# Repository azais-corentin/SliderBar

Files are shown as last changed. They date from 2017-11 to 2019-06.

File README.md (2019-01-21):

<p align="center">
  <a href="https://github.com/Haellsigh/SliderBar">
    
  </a>

  <h3 align="center">SliderBar</h3>

  <p align="center">
    Motorized keyboard slider with an advanced controller.
  </p>
</p>

## Table of contents

- [What's that](#whats-that)
- [Quick start](#quick-start)
- [Documentation](#documentation)
- [Copyright and license](#copyright-and-license)

## What's that

It's a keyboard slider that connects to your computer using USB.
Depending on the plugins you loaded using the desktop application, you can use your slider to execute some actions.
Here are some examples:
- Switch chrome tabs easily in one swipe.
- Switch between opened applications.
- Scroll through a window.
- Control sliders and other things in applications like Photoshop or After Effects.

## Quick start

### Get started as a user

Too early in the development for that.

### Get started with development

Follow this short guide:

- Clone the repo: `git clone --recursive https://github.com/haellsigh/SliderBar.git`
- If you want to develop for desktop:
  - Install Qt Creator with Qt > 4.0
- If you want to develop for embedded:
  - Install [PlatformIO](https://platformio.org/platformio-ide) for [VSCode](https://code.visualstudio.com/) or [Atom](https://atom.io/).

Read the [Getting started page](https://sliderbar.readthedocs.io/en/latest/) for information on the SliderBar, example plugins and more.

## Documentation

SliderBar's documentation, included in this repo in the `docs/` directory, is built
with [Sphinx](http://www.sphinx-doc.org/en/master/) and
[Doxygen](http://www.doxygen.nl/) and publicly hosted ReadTheDocs at <https://sliderbar.readthedocs.io/en/latest/>.

## Copyright and license

Code and documentation copyright 2017-2018
[Haellsigh](https://github.com/haellsigh). Code and
docs released under the [MIT
License](https://github.com/Haellsigh/SliderBar/blob/master/LICENSE).

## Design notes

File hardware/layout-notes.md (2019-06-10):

# PCB Layout notes

## 3.3V Regulator (LP2985-33)

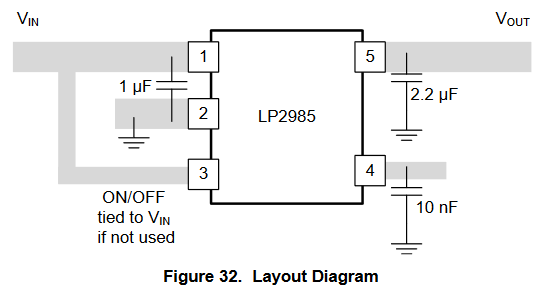
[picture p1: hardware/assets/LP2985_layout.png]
LP2985_layout


* Ceramics capacitor are preferred.
* Input capacitor within 1cm of input pin. Minimum 1uF.
* Values in the schematic are minimums.

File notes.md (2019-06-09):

# Notes

These notes cover both the software and hardware development.

## Oscilloscope

Hantek 6022BL with OpenHantek

## Test points

* Round holes for pins
* Small loops to put a probe

## LEDs

* For GPIO LEDs, connect the LED to 3V3, use GPIO to pull down.
* Power LED on the 3v3.
* Add a LED to display errors! Use it with the `Error_Handler`:

```c
static void Error_Handler(void)
{
  /* Turn LED3 on */
  BSP_LED_On(LED3);
  while (1)
  {
  }
}
```

* Add at least 2 other LEDs to display various informations (low power LEDs).

## USB

* The STM32 integrates pull up resistor for USB_DP line. It can be toggled with `HAL_PCD_DevDisconnect` and `HAL_PCD_DevConnect`. See at page 882 of reference.
* ESD protection should be as close to the MCU as possible.
* Integrate overcurrent protection using a `STMPS2151STR`.
* Use USB type C receptacle? See `usb2_0_to_usb_c_migration.pdf` page 16.
* Eventually use DFU to program the device (DFU in bootloader) while still using VCP to communicate (USB CDC in flash). See [STM32 USB VCP and DFU](https://community.st.com/s/question/0D50X00009XkfzkSAB/stm32f4-usb-vcp-cdc-and-dfu).

## DFU Principle

The Internal flash memory memory is split as follows:

* DFU area located in [0x08000000 : USBD_DFU_APP_DEFAULT_ADD-1]: Only read access
* Application area located in [USBD_DFU_APP_DEFAULT_ADD : Device's end address : Read, Write, and Erase access

Configure a GPIO input. If pressed at boot, go to DFU mode, otherwise normal application. Check the example: `Applications\USB_Device\DFU_Standalone`. There is an error in the example, line 88 of `main.c` should be 'If the button is not pressed'.

## Timers

* To get a frequency for the pwm, compute the prescaler from the SystemCoreClock if APB1 clock is SystemCoreClock. Example for 10000 Hz:

```c++
uint8_t period = 255;
uint16_t prescaler = (uint16_t)(SystemCoreClock / ((period + 1) * 10000)) - 1;
```

* Add test pin(s) to the PWM output

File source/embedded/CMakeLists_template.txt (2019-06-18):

#${templateWarning}
SET(CMAKE_SYSTEM_NAME Generic)
SET(CMAKE_SYSTEM_VERSION 1)
cmake_minimum_required(VERSION 3.7)

# specify cross compilers and tools
SET(CMAKE_C_COMPILER_WORKS 1)
SET(CMAKE_C_COMPILER arm-none-eabi-gcc)
SET(CMAKE_CXX_COMPILER_WORKS 1)
SET(CMAKE_CXX_COMPILER arm-none-eabi-g++)
set(CMAKE_ASM_COMPILER  arm-none-eabi-gcc)
set(CMAKE_AR arm-none-eabi-ar)
set(CMAKE_OBJCOPY arm-none-eabi-objcopy)
set(CMAKE_OBJDUMP arm-none-eabi-objdump)
set(SIZE arm-none-eabi-size)

SET(LINKER_SCRIPT $${CMAKE_SOURCE_DIR}/${linkerScript})

#Uncomment for hardware floating point
#SET(FPU_FLAGS "-mfloat-abi=hard -mfpu=fpv4-sp-d16")
#add_definitions(-DARM_MATH_CM4 -DARM_MATH_MATRIX_CHECK -DARM_MATH_ROUNDING -D__FPU_PRESENT=1)

#Uncomment for software floating point
#SET(FPU_FLAGS "-mfloat-abi=soft")

SET(COMMON_FLAGS
    "-mcpu=${mcpu} $${FPU_FLAGS} -mthumb -mthumb-interwork -ffunction-sections -fdata-sections \
    -g -fno-common -fmessage-length=0 ${linkerFlags}")

SET(CMAKE_CXX_FLAGS_INIT "$${COMMON_FLAGS} -std=c++14")
SET(CMAKE_C_FLAGS_INIT "$${COMMON_FLAGS} -std=gnu99")
SET(CMAKE_EXE_LINKER_FLAGS_INIT "-Wl,-gc-sections,--print-memory-usage -T $${LINKER_SCRIPT}")

PROJECT(${projectName} C CXX ASM)
set(CMAKE_CXX_STANDARD 14)

#add_definitions(-DARM_MATH_CM4 -DARM_MATH_MATRIX_CHECK -DARM_MATH_ROUNDING -D__FPU_PRESENT=1)
add_definitions(${defines})

set(PRJ_SOURCES "../common/protocol/protocol_definition.cpp" "../common/protocol/messages/sliderbar.pb.c" "../common/nanopb/pb_common.c" "../common/nanopb/pb_decode.c" "../common/nanopb/pb_encode.c")
file(GLOB_RECURSE SOURCES ${sources})

include_directories(${includes} Inc/USB ../common ../common/nanopb)

add_executable($${PROJECT_NAME}.elf $${SOURCES} $${PRJ_SOURCES} $${LINKER_SCRIPT})

set(CMAKE_EXE_LINKER_FLAGS
    "$${CMAKE_EXE_LINKER_FLAGS} -Wl,-Map=$${PROJECT_BINARY_DIR}/$${PROJECT_NAME}.map")

set(HEX_FILE $${PROJECT_BINARY_DIR}/$${PROJECT_NAME}.hex)
set(BIN_FILE $${PROJECT_BINARY_DIR}/$${PROJECT_NAME}.bin)

add_custom_command(TARGET $${PROJECT_NAME}.elf POST_BUILD
        COMMAND $${CMAKE_OBJCOPY} -Oihex $<TARGET_FILE:$${PROJECT_NAME}.elf> $${HEX_FILE}
        COMMAND $${CMAKE_OBJCOPY} -Obinary $<TARGET_FILE:$${PROJECT_NAME}.elf> $${BIN_FILE}
        COMMENT "Building $${HEX_FILE}
Building $${BIN_FILE}")

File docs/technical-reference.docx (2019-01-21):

# SliderBAR

# Technical REFERENCE

# Motorized keyboard slider with an advanced controller

Features

- Motorized fader composed of a linear potentiometer and a belt and pulley system to move the fader
- Open hardware and open source
- USB Powered (USB Mini B connector)
- Desktop configuration GUI
- Programmable plugins
- USB CDC Virtual Serial Port for plug-n-play on any PC

Hardware specifications

- USB Mini B connector (power & communications)
- STM32F072C8T6 MCU
- 5-pin ST-Link V2 programming interface
- 5V to 3.3V regulator (MIC5205-33)
- 5V to 10V boost converter (MT3608) with trimmable potentiometer
- TB6612FNG motor driver (max 1.2 A)
- Pin headers for debug, motor out, and potentiometer in

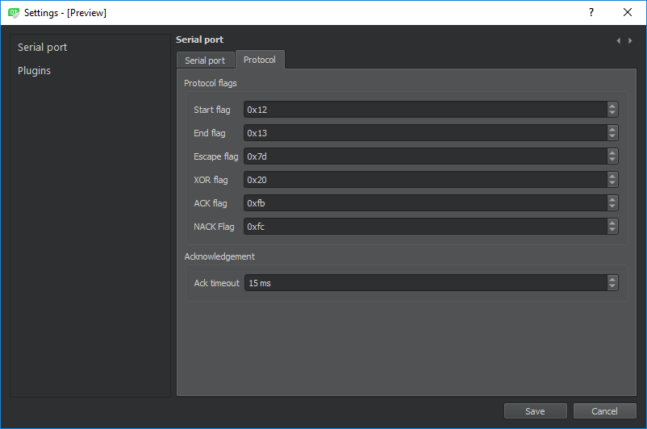
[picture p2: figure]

Figure 1. Configuration window

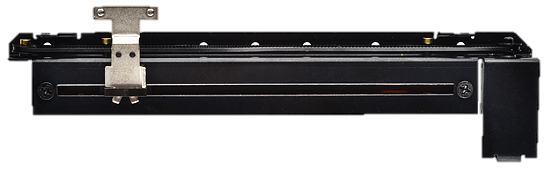
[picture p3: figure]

Software specifications

Figure 2. Motorized fader

- Desktop side:
  - Written in C++ with Qt for the GUI
  - IDE: Qt Creator
  - Base application allows user to manage settings, connect, load plugins and set activators for each plugin
  - Base application does nothing, the plugins parse the slider’s input
  - Each plugin receives the SliderBar’s position and can use the app’s API to execute actions
- Embedded side:
  - Written in C++ with STM32CubeHal
  - IDE: Visual Studio Code with PlatformIO
  - Lightweight communication protocol.

## Table of contents

## 1 Introduction

### 1.1 Description

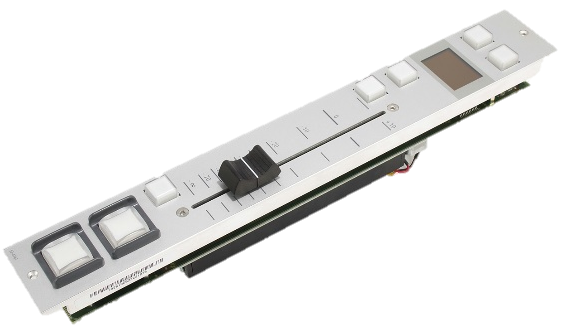
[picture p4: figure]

#### 1.1.1 General description

The SliderBar is a keyboard slider that mounts to or sits near your keyboard. It is based on a motorized fader as originally used in Audio mixer tables (See Figure 3).

Figure 3. 52-4261B Motor Fader Module

## 2 Hardware

### 2.1 General description

The USB connector provides power and communications to the MCU and motor.

The host (PC) controls the SliderBar via a lightweight USB communications protocol.

The STM32F072C8T6 MCU processes the commands and controls the motor accordingly through the TB6612FNG motor driver.

Position is read using the potentiometer provided in the fader.

The hardware consists of different modules:

- Microcontroller
- USB Mini B connector
- Programming interface
- 3.3V regulator
- 10V boost converter
- Motor driver
- Pin headers for debug, motor out, and potentiometer in

### 2.2 Modules description

#### 2.2.1 Microcontroller

The microcontroller used is the STM32F072C8T6.

It was selected because it is cheap, low power, supports crystal-less USB 2.0 FS and is quite powerful enough.

#### 2.2.2 USB Mini B connector

It is stronger than a Micro B connector.

#### 2.2.3 Programming interface

Programming is done using an ST-Link V2 through the Serial Wire Debug (SWD) interface.

There are 5 exposed pins: SWDIO, GND, SWCLK, V_(PP) , NRST (See Figure 4. Debug header).

SWCLK is the clock of the SWD, SWDIO is the input output of the SWD.

V_(PP) is the programming voltage. Connect it to the 5V of the ST-Link V2.

Note: Do no exceed the limits of 3.5V and 8V (See Table 1. General operating conditions).

#### 2.2.4 3.3V regulator

#### 2.2.5 10V boost converter

#### 2.2.6 Motor driver

#### 2.2.7 Pin headers

##### 2.2.7.1 Debug

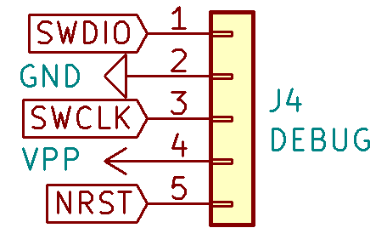
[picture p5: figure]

##### 2.2.7.2 Motor out

##### 2.2.7.3 Potentiometer in

Figure 4. Debug header

## 3 Software

## 4 Electrical characteristics

### 4.1 Typical values

Unless otherwise specified, typical data are based on T_A = 25 °C, V_(DD) = 5V.

### 4.2 Operating conditions

#### 4.2.1 General operating conditions

Table 1. General operating conditions

Symbol | Parameter | Conditions | Min | Typical | Max | Unit
V_(PP) | Programming supply voltage | - | 3.5 | 5 | 8 | V
V_(BUS) | USB supply voltage | - | 4.75 | 5 | 5.25 | V

#### 4.2.2 Supply current characteristics

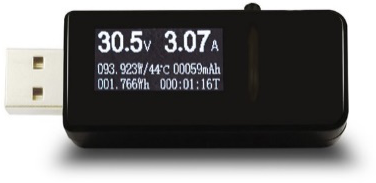
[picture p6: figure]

The current consumption is a function of several parameters and factors such as microcontroller state (run, sleep) and motor state (full speed, stop).

The current consumption is measured using a cheap USB volt/amp meter. See Figure 5.

Figure 5. USB Voltmeter

Table 2. Supply current characteristics

Symbol | Parameter | Conditions | Min | Typical | Max | Unit
I_(idle) | Idle current at V_(BUS) | - | 8 | 10 | 20 | mA
I_(average) | Average current at V_(BUS) | - | 8 | 100 | 500 | mA

## 5 Revision history

Revision history

Electrical characteristics

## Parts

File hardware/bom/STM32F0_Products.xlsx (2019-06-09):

Microcontrollers & Microprocessors / STM32 32-bit Arm Cortex MCUs / STM32 Mainstream MCUs / STM32F0 Series / STM32F0x0 Value Line
Part Number | Package | Core | Operating Frequency (MHz) | Flash Size (kB) | RAM Size | USB Type
STM32F030C6 (https://www.st.com/en/product/stm32f030c6.html) | LQFP 48 7x7x1.4 | Arm Cortex-M0 | 48 | 32 | 4 | -
STM32F030C8 (https://www.st.com/en/product/stm32f030c8.html) | LQFP 48 7x7x1.4 | Arm Cortex-M0 | 48 | 64 | 8 | -
STM32F030CC (https://www.st.com/en/product/stm32f030cc.html) | LQFP 48 7x7x1.4 | Arm Cortex-M0 | 48 | 256 | 32 | -
STM32F030F4 (https://www.st.com/en/product/stm32f030f4.html) | TSSOP 20 | Arm Cortex-M0 | 48 | 16 | 4 | -
STM32F030K6 (https://www.st.com/en/product/stm32f030k6.html) | LQFP 32 7x7x1.4 | Arm Cortex-M0 | 48 | 32 | 4 | -
STM32F030R8 (https://www.st.com/en/product/stm32f030r8.html) | LQFP 64 10x10x1.4 | Arm Cortex-M0 | 48 | 64 | 8 | -
STM32F030RC (https://www.st.com/en/product/stm32f030rc.html) | LQFP 64 10x10x1.4 | Arm Cortex-M0 | 48 | 256 | 32 | -
STM32F031C4 (https://www.st.com/en/product/stm32f031c4.html) | LQFP 48 7x7x1.4 | Arm Cortex-M0 | 48 | 16 | 4 | -
STM32F031C6 (https://www.st.com/en/product/stm32f031c6.html) | LQFP 48 7x7x1.4 | Arm Cortex-M0 | 48 | 32 | 4 | -
STM32F031E6 (https://www.st.com/en/product/stm32f031e6.html) | WLCSP 25L P 0.4 MM DIE 444 | Arm Cortex-M0 | 48 | 32 | 4 | -
STM32F031F4 (https://www.st.com/en/product/stm32f031f4.html) | TSSOP 20 | Arm Cortex-M0 | 48 | 16 | 4 | -
STM32F031F6 (https://www.st.com/en/product/stm32f031f6.html) | TSSOP 20 | Arm Cortex-M0 | 48 | 32 | 4 | -
STM32F031G4 (https://www.st.com/en/product/stm32f031g4.html) | UFQFPN 28 4x4x0.55 | Arm Cortex-M0 | 48 | 16 | 4 | -
STM32F031G6 (https://www.st.com/en/product/stm32f031g6.html) | UFQFPN 28 4x4x0.55 | Arm Cortex-M0 | 48 | 32 | 4 | -
STM32F031K4 (https://www.st.com/en/product/stm32f031k4.html) | UFQFPN 32 5x5x0.55 | Arm Cortex-M0 | 48 | 16 | 4 | -
STM32F031K6 (https://www.st.com/en/product/stm32f031k6.html) | LQFP 32 7x7x1.4,UFQFPN 32 5x5x0.55 | Arm Cortex-M0 | 48 | 32 | 4 | -
STM32F038C6 (https://www.st.com/en/product/stm32f038c6.html) | LQFP 48 7x7x1.4 | Arm Cortex-M0 | 48 | 32 | 4 | -
STM32F038E6 (https://www.st.com/en/product/stm32f038e6.html) | WLCSP 25L P 0.4 MM DIE 444 | Arm Cortex-M0 | 48 | 32 | 4 | -
STM32F038F6 (https://www.st.com/en/product/stm32f038f6.html) | TSSOP 20 | Arm Cortex-M0 | 48 | 32 | 4 | -
STM32F038G6 (https://www.st.com/en/product/stm32f038g6.html) | UFQFPN 28 4x4x0.55 | Arm Cortex-M0 | 48 | 32 | 4 | -
STM32F038K6 (https://www.st.com/en/product/stm32f038k6.html) | UFQFPN 32 5x5x0.55 | Arm Cortex-M0 | 48 | 32 | 4 | -
STM32F070CB (https://www.st.com/en/product/stm32f070cb.html) | LQFP 48 7x7x1.4 | Arm Cortex-M0 | 48 | 128 | 16 | USB Device
STM32F070RB (https://www.st.com/en/product/stm32f070rb.html) | LQFP 64 10x10x1.4 | Arm Cortex-M0 | 48 | 128 | 16 | USB Device
STM32F072CB (https://www.st.com/en/product/stm32f072cb.html) | LQFP 48 7x7x1.4,UFQFPN 48 7x7x0.55,WLCSP 49L DIE 448 P 0.4 MM | Arm Cortex-M0 | 48 | 128 | 16 | USB Device
STM32F072RB (https://www.st.com/en/product/stm32f072rb.html) | LQFP 64 10x10x1.4,UFBGA 5X5X0.6 64L P 0.5 MM | Arm Cortex-M0 | 48 | 128 | 16 | USB Device
STM32F072VB (https://www.st.com/en/product/stm32f072vb.html) | LQFP 100 14x14x1.4,UFBGA 100 7x7x0.6 | Arm Cortex-M0 | 48 | 128 | 16 | USB Device
STM32F078CB (https://www.st.com/en/product/stm32f078cb.html) | LQFP 48 7x7x1.4,UFQFPN 48 7x7x0.55,WLCSP 49L DIE 448 P 0.4 MM | Arm Cortex-M0 | 48 | 128 | 16 | USB Device
STM32F078RB (https://www.st.com/en/product/stm32f078rb.html) | LQFP 64 10x10x1.4,UFBGA 5X5X0.6 64L P 0.5 MM | Arm Cortex-M0 | 48 | 128 | 16 | USB Device
STM32F078VB (https://www.st.com/en/product/stm32f078vb.html) | LQFP 100 14x14x1.4,UFBGA 100 7x7x0.6 | Arm Cortex-M0 | 48 | 128 | 16 | USB Device
STM32F042C4 (https://www.st.com/en/product/stm32f042c4.html) | LQFP 48 7x7x1.4,UFQFPN 48 7x7x0.55 | Arm Cortex-M0 | 48 | 16 | 6 | USB Device
STM32F042F4 (https://www.st.com/en/product/stm32f042f4.html) | TSSOP 20 | Arm Cortex-M0 | 48 | 16 | 6 | USB Device
STM32F042G4 (https://www.st.com/en/product/stm32f042g4.html) | UFQFPN 28 4x4x0.55 | Arm Cortex-M0 | 48 | 16 | 6 | USB Device
STM32F042K4 (https://www.st.com/en/product/stm32f042k4.html) | LQFP 32 7x7x1.4,UFQFPN 32 5x5x0.55 | Arm Cortex-M0 | 48 | 16 | 6 | USB Device
STM32F051C4 (https://www.st.com/en/product/stm32f051c4.html) | LQFP 48 7x7x1.4,UFQFPN 48 7x7x0.55 | Arm Cortex-M0 | 48 | 16 | 8 | -
STM32F051C6 (https://www.st.com/en/product/stm32f051c6.html) | LQFP 48 7x7x1.4,UFQFPN 48 7x7x0.55 | Arm Cortex-M0 | 48 | 32 | 8 | -
STM32F051C8 (https://www.st.com/en/product/stm32f051c8.html) | LQFP 48 7x7x1.4,UFQFPN 48 7x7x0.55 | Arm Cortex-M0 | 48 | 64 | 8 | -
STM32F051K4 (https://www.st.com/en/product/stm32f051k4.html) | LQFP 32 7x7x1.4,UFQFPN 32 5x5x0.55 | Arm Cortex-M0 | 48 | 16 | 8 | -
STM32F051K6 (https://www.st.com/en/product/stm32f051k6.html) | LQFP 32 7x7x1.4,UFQFPN 32 5x5x0.55 | Arm Cortex-M0 | 48 | 32 | 8 | -
STM32F051K8 (https://www.st.com/en/product/stm32f051k8.html) | LQFP 32 7x7x1.4,UFQFPN 32 5x5x0.55 | Arm Cortex-M0 | 48 | 64 | 8 | -
STM32F051R4 (https://www.st.com/en/product/stm32f051r4.html) | LQFP 64 10x10x1.4 | Arm Cortex-M0 | 48 | 16 | 8 | -
STM32F051R6 (https://www.st.com/en/product/stm32f051r6.html) | LQFP 64 10x10x1.4 | Arm Cortex-M0 | 48 | 32 | 8 | -
STM32F051R8 (https://www.st.com/en/product/stm32f051r8.html) | LQFP 64 10x10x1.4,UFBGA 5X5X0.6 64L P 0.5 MM | Arm Cortex-M0 | 48 | 64 | 8 | -
STM32F051T8 (https://www.st.com/en/product/stm32f051t8.html) | WLCSP 36L P 0.4 MM DIE 440 | Arm Cortex-M0 | 48 | 64 | 8 | -
STM32F058C8 (https://www.st.com/en/product/stm32f058c8.html) | UFQFPN 48 7x7x0.55 | Arm Cortex-M0 | 48 | 64 | 8 | -
STM32F058R8 (https://www.st.com/en/product/stm32f058r8.html) | LQFP 64 10x10x1.4,UFBGA 5X5X0.6 64L P 0.5 MM | Arm Cortex-M0 | 48 | 64 | 8 | -
STM32F058T8 (https://www.st.com/en/product/stm32f058t8.html) | WLCSP 36L P 0.4 MM DIE 440 | Arm Cortex-M0 | 48 | 64 | 8 | -
STM32F042C6 (https://www.st.com/en/product/stm32f042c6.html) | LQFP 48 7x7x1.4,UFQFPN 48 7x7x0.55 | Arm Cortex-M0 | 48 | 32 | 6 | USB Device
STM32F042F6 (https://www.st.com/en/product/stm32f042f6.html) | TSSOP 20 | Arm Cortex-M0 | 48 | 32 | 6 | USB Device
STM32F042G6 (https://www.st.com/en/product/stm32f042g6.html) | UFQFPN 28 4x4x0.55 | Arm Cortex-M0 | 48 | 32 | 6 | USB Device
STM32F042K6 (https://www.st.com/en/product/stm32f042k6.html) | LQFP 32 7x7x1.4,UFQFPN 32 5x5x0.55 | Arm Cortex-M0 | 48 | 32 | 6 | USB Device
STM32F071C8 (https://www.st.com/en/product/stm32f071c8.html) | LQFP 48 7x7x1.4,UFQFPN 48 7x7x0.55 | Arm Cortex-M0 | 48 | 64 | 16 | -
STM32F071CB (https://www.st.com/en/product/stm32f071cb.html) | LQFP 48 7x7x1.4,UFQFPN 48 7x7x0.55,WLCSP 49L DIE 448 P 0.4 MM | Arm Cortex-M0 | 48 | 128 | 16 | -
STM32F071RB (https://www.st.com/en/product/stm32f071rb.html) | LQFP 64 10x10x1.4 | Arm Cortex-M0 | 48 | 128 | 16 | -
STM32F071V8 (https://www.st.com/en/product/stm32f071v8.html) | LQFP 100 14x14x1.4,UFBGA 100 7x7x0.6 | Arm Cortex-M0 | 48 | 64 | 16 | -
STM32F071VB (https://www.st.com/en/product/stm32f071vb.html) | LQFP 100 14x14x1.4,UFBGA 100 7x7x0.6 | Arm Cortex-M0 | 48 | 128 | 16 | -
STM32F042T6 (https://www.st.com/en/product/stm32f042t6.html) | WLCSP 36L DIE 445 P 0.4 MM | Arm Cortex-M0 | 48 | 32 | 6 | USB Device
STM32F048C6 (https://www.st.com/en/product/stm32f048c6.html) | UFQFPN 48 7x7x0.55 | Arm Cortex-M0 | 48 | 32 | 6 | USB Device
STM32F048G6 (https://www.st.com/en/product/stm32f048g6.html) | UFQFPN 28 4x4x0.55 | Arm Cortex-M0 | 48 | 32 | 6 | USB Device
STM32F048T6 (https://www.st.com/en/product/stm32f048t6.html) | WLCSP 36L DIE 445 P 0.4 MM | Arm Cortex-M0 | 48 | 32 | 6 | USB Device
STM32F070C6 (https://www.st.com/en/product/stm32f070c6.html) | LQFP 48 7x7x1.4 | Arm Cortex-M0 | 48 | 32 | 6 | USB Device
STM32F070F6 (https://www.st.com/en/product/stm32f070f6.html) | TSSOP 20 | Arm Cortex-M0 | 48 | 32 | 6 | USB Device
STM32F072C8 (https://www.st.com/en/product/stm32f072c8.html) | LQFP 48 7x7x1.4,UFQFPN 48 7x7x0.55 | Arm Cortex-M0 | 48 | 64 | 16 | USB Device
STM32F072R8 (https://www.st.com/en/product/stm32f072r8.html) | LQFP 64 10x10x1.4 | Arm Cortex-M0 | 48 | 64 | 16 | USB Device
STM32F072V8 (https://www.st.com/en/product/stm32f072v8.html) | LQFP 100 14x14x1.4,UFBGA 100 7x7x0.6 | Arm Cortex-M0 | 48 | 64 | 16 | USB Device
STM32F091CB (https://www.st.com/en/product/stm32f091cb.html) | LQFP 48 7x7x1.4,UFQFPN 48 7x7x0.55 | Arm Cortex-M0 | 48 | 128 | 32 | -
STM32F091CC (https://www.st.com/en/product/stm32f091cc.html) | LQFP 48 7x7x1.4,UFQFPN 48 7x7x0.55 | Arm Cortex-M0 | 48 | 256 | 32 | -
STM32F091RB (https://www.st.com/en/product/stm32f091rb.html) | LQFP 64 10x10x1.4 | Arm Cortex-M0 | 48 | 128 | 32 | -
STM32F091RC (https://www.st.com/en/product/stm32f091rc.html) | LQFP 64 10x10x1.4,UFBGA 5X5X0.6 64L P 0.5 MM,WLCSP 64L DIE 442 P 0.4 MM | Arm Cortex-M0 | 48 | 256 | 32 | -
STM32F091VB (https://www.st.com/en/product/stm32f091vb.html) | LQFP 100 14x14x1.4 | Arm Cortex-M0 | 48 | 128 | 32 | -
STM32F091VC (https://www.st.com/en/product/stm32f091vc.html) | LQFP 100 14x14x1.4,UFBGA 100 7x7x0.6 | Arm Cortex-M0 | 48 | 256 | 32 | -
STM32F098CC (https://www.st.com/en/product/stm32f098cc.html) | LQFP 48 7x7x1.4,UFQFPN 48 7x7x0.55 | Arm Cortex-M0 | 48 | 256 | 32 | -
STM32F098RC (https://www.st.com/en/product/stm32f098rc.html) | LQFP 64 10x10x1.4,UFBGA 5X5X0.6 64L P 0.5 MM,WLCSP 64L DIE 442 P 0.4 MM | Arm Cortex-M0 | 48 | 256 | 32 | -
STM32F098VC (https://www.st.com/en/product/stm32f098vc.html) | LQFP 100 14x14x1.4,UFBGA 100 7x7x0.6 | Arm Cortex-M0 | 48 | 256 | 32 | -

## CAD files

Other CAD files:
hardware/3d/EN_ISO_4032_M2_STEEL_GRADE_A_HEXAGON_NUT.CATPart
hardware/3d/Frame.CATPart
hardware/3d/Gearmotor.CATPart
hardware/3d/Hex_spacer.CATPart
hardware/3d/ISO_7046-1_M2x16-H_STEEL_GRADE_A_COUNTERSUNK_FLAT_HEAD_SCREW.CATPart
hardware/3d/ISO_7046-2_M2x5-H2_STEEL_GRADE_A_COUNTERSUNK_FLAT_HEAD_SCREW.CATPart
hardware/3d/KeyboardCase.CATPart
hardware/3d/Lever support.CATPart
hardware/3d/Lever.CATPart
hardware/3d/Motorized_Potentiometer.CATProduct
hardware/3d/SliderBar.CATProduct
hardware/3d/SliderBar_Demo.CATProduct
hardware/3d/SliderBar_pcb.CATProduct
hardware/3d/SliderBar_pcb/COMPOUND.CATPart
hardware/3d/SliderBar_pcb/COMPOUND_1.CATPart
hardware/3d/SliderBar_pcb/CP_EIA-6032-28_Kemet-C.CATProduct
hardware/3d/SliderBar_pcb/C_0805_2012Metric.CATProduct
hardware/3d/SliderBar_pcb/D_SMA.CATProduct
hardware/3d/SliderBar_pcb/JST_GH_BM05B-GHS-TBT_1x05-1MP_P1.25mm_Vertical.CATProduct
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

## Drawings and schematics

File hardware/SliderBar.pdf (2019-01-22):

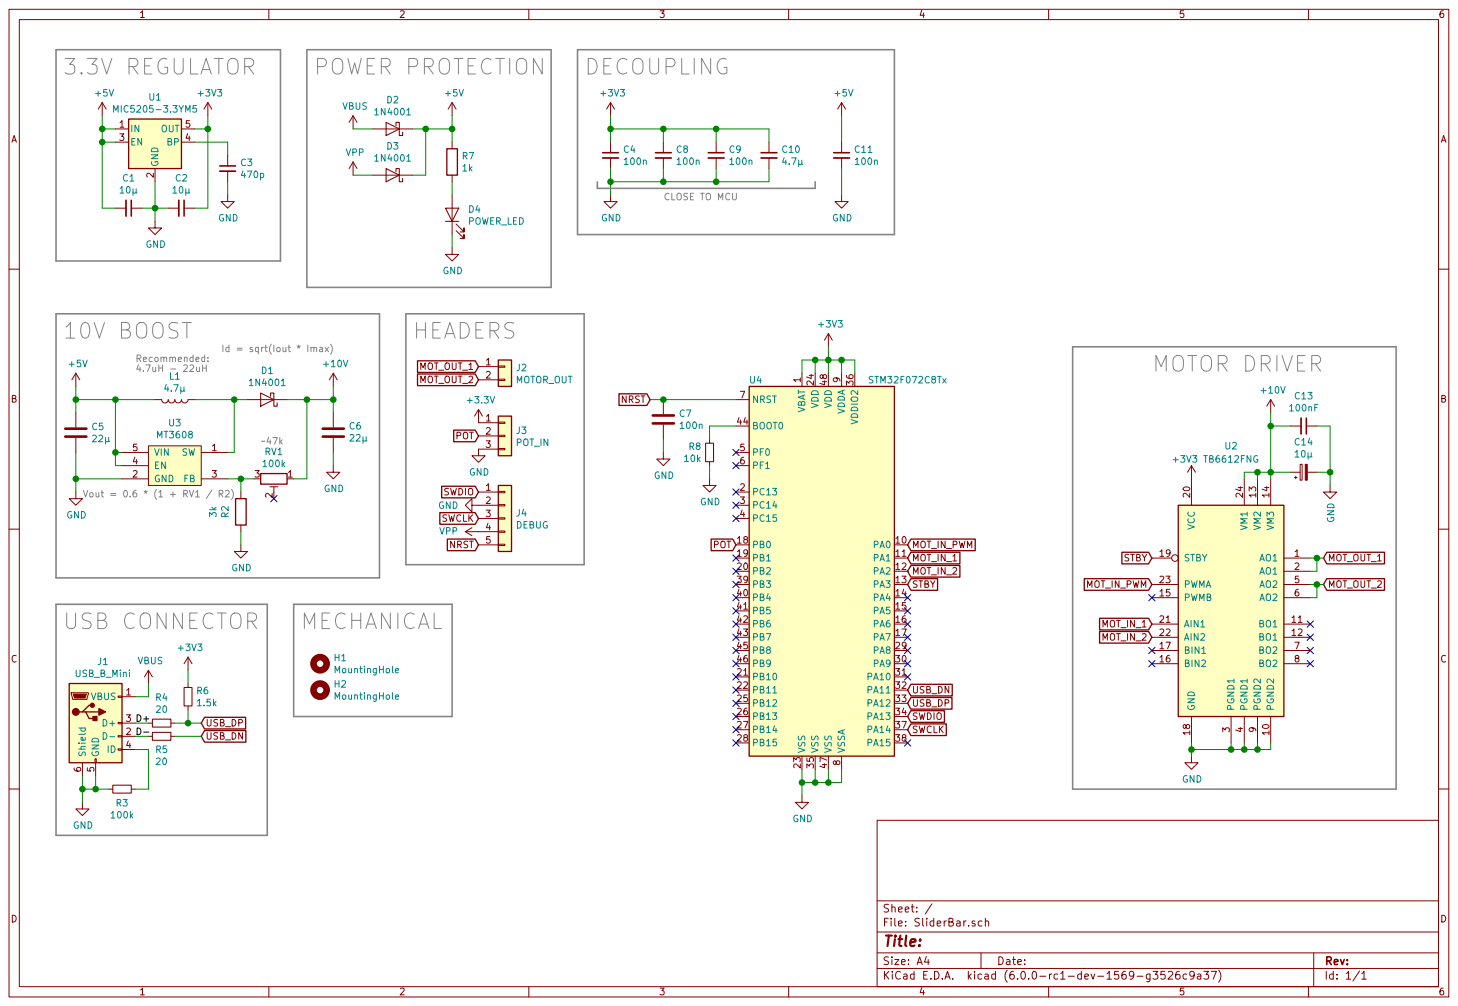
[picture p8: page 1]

2 EN 3 BP 4 OUT 5 U1 MIC5205-3.3YM5 +3V3 3.3V REGULATOR

HEADERS
SWCLK NRST GND MOT_OUT_1 MOT_OUT_2 POTGND

9 VDDIO2 36 VSS 23 VSS 35 VSS 47 VSSA

Id: 1/1 Title: File: SliderBar.sch Sheet: /

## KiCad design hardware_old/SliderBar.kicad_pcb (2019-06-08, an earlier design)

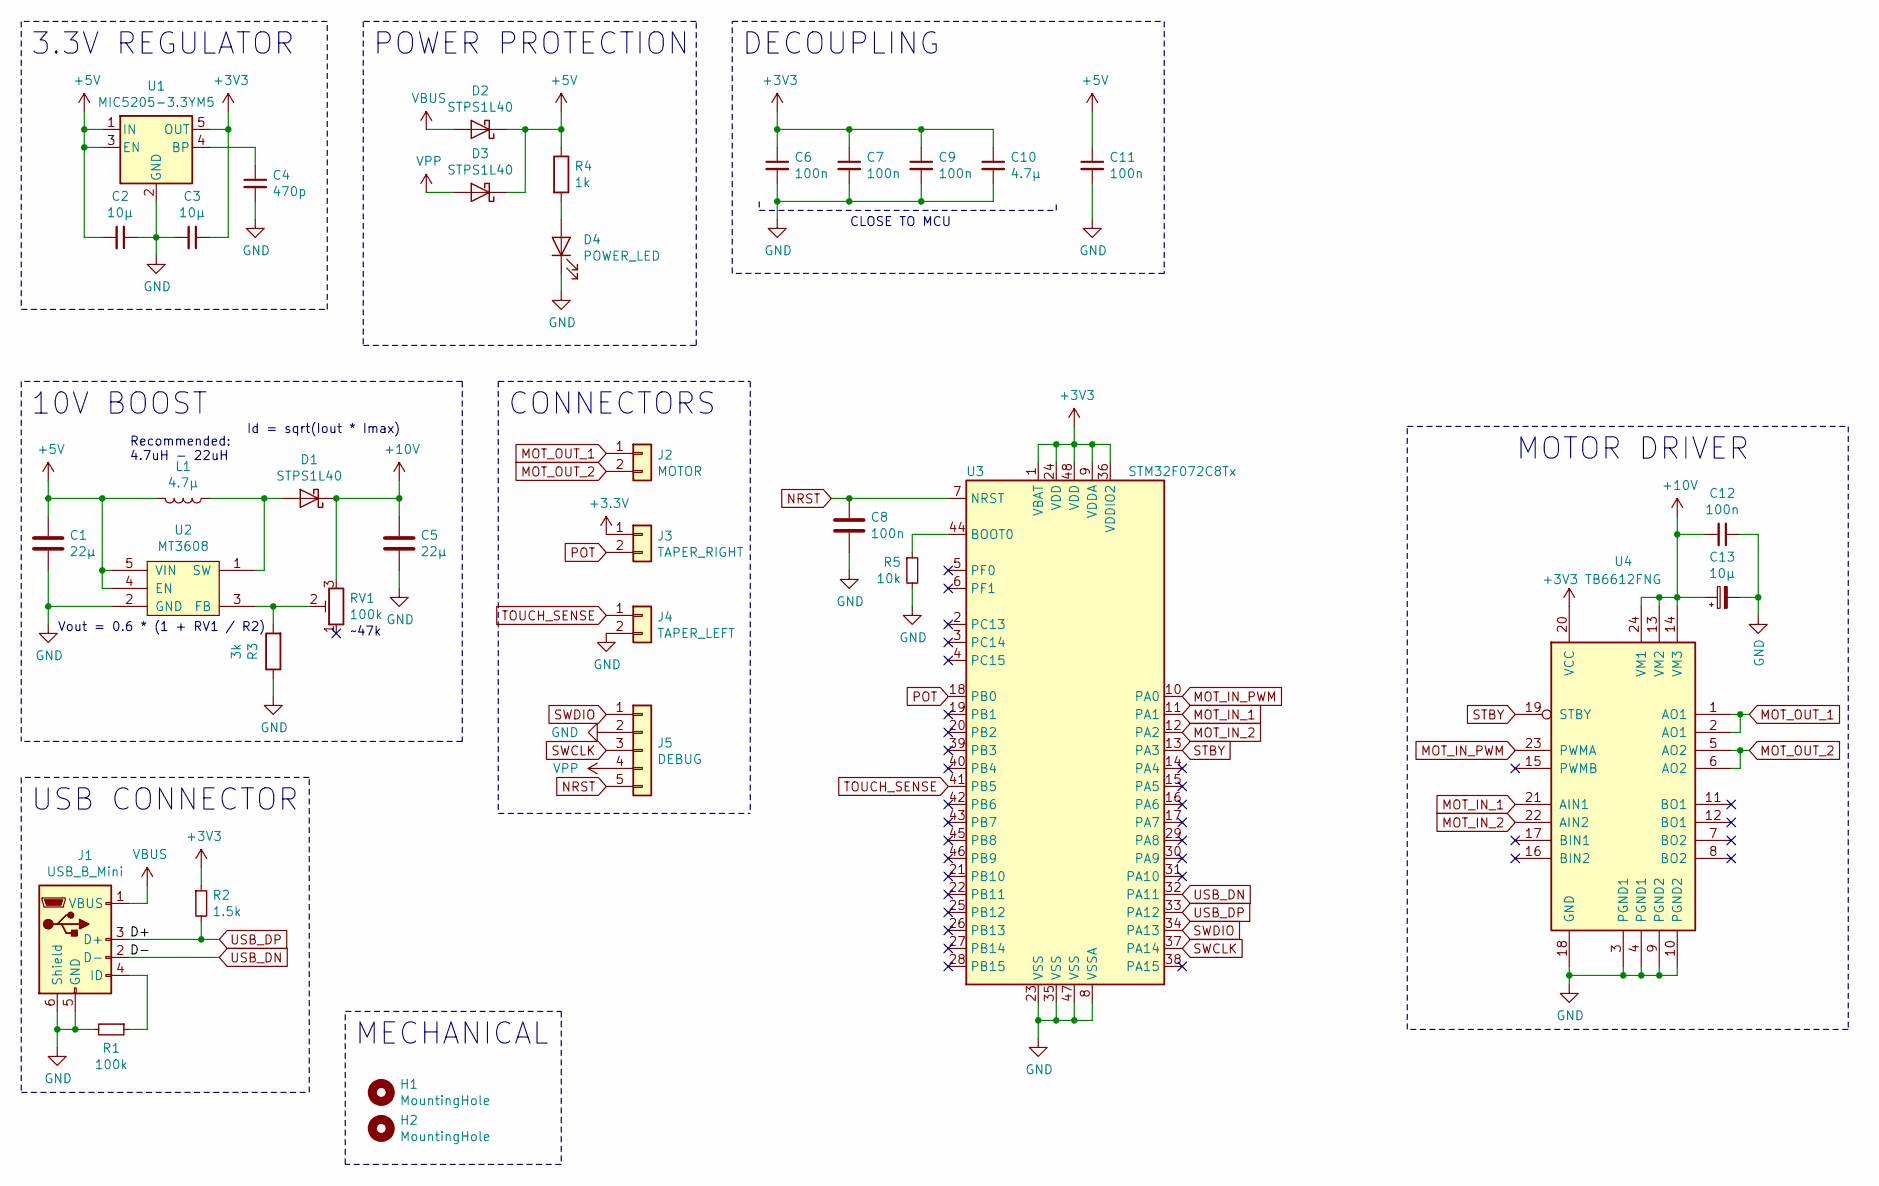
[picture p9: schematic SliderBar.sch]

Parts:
C1, C5: 22µ; C_0805_2012Metric_Pad1.15x1.40mm_HandSolder
C2, C3: 10µ; C_0805_2012Metric_Pad1.15x1.40mm_HandSolder
C4: 470p; C_0805_2012Metric_Pad1.15x1.40mm_HandSolder
C6, C7, C8, C9, C11, C12: 100n; C_0805_2012Metric_Pad1.15x1.40mm_HandSolder
C10: 4.7µ; C_0805_2012Metric_Pad1.15x1.40mm_HandSolder
C13: 10µ; CP_EIA-6032-28_Kemet-C_Pad2.25x2.35mm_HandSolder
D1, D2, D3: STPS1L40; D_SMA
D4: POWER_LED; LED_1206_3216Metric_Pad1.42x1.75mm_HandSolder
H1, H2: MountingHole; MountingHole_2.2mm_M2_Pad
J1: USB_B_Mini; USB_Mini-B_Lumberg_2486_01_Horizontal
J2: MOTOR; JST_GH_SM02B-GHS-TB_1x02-1MP_P1.25mm_Horizontal
J3: TAPER_RIGHT; JST_GH_SM02B-GHS-TB_1x02-1MP_P1.25mm_Horizontal
J4: TAPER_LEFT; JST_GH_SM02B-GHS-TB_1x02-1MP_P1.25mm_Horizontal
J5: DEBUG; JST_GH_BM05B-GHS-TBT_1x05-1MP_P1.25mm_Vertical
L1: 4.7µ; L_7.3x7.3_H3.5
R1: 100k; R_0805_2012Metric_Pad1.15x1.40mm_HandSolder
R2: 1.5k; R_0805_2012Metric_Pad1.15x1.40mm_HandSolder
R3: 3k; R_0805_2012Metric_Pad1.15x1.40mm_HandSolder
R4: 1k; R_0805_2012Metric_Pad1.15x1.40mm_HandSolder
R5: 10k; R_0805_2012Metric_Pad1.15x1.40mm_HandSolder
RV1: 100k; AB2_POT_TRIM
U1: MIC5205-3.3YM5; SOT-23-5
U2: MT3608; SOT-23-6_Handsoldering
U3: STM32F072C8Tx; LQFP-48_7x7mm_P0.5mm
U4: TB6612FNG; SSOP-24_5.3x8.2mm_P0.65mm

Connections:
+5V: C1.1, C2.2, C11.1, D2.1 (K), D3.1 (K), L1.2, R4.1, U1.1 (IN), U1.3 (EN), U2.4 (EN), U2.5 (VIN)
+10V: C5.2, C12.2, C13.1, D1.1 (K), RV1.3, U4.13 (VM2), U4.14 (VM3), U4.24 (VM1)
GND: C1.2, C2.1, C3.2, C4.2, C5.1, C6.2, C7.2, C8.2, C9.2, C10.2, C11.2, C12.1, C13.2, D4.1 (K), J1.5 (GND), J1.6 (Shield), J4.2, J5.2, R1.2, R3.1, R5.2, U1.2 (GND), U2.2 (GND), U3.8 (VSSA), U3.23 (VSS), U3.35 (VSS), U3.47 (VSS), U4.3 (PGND1), U4.4 (PGND1), U4.9 (PGND2), U4.10 (PGND2), U4.18 (GND)
MOT_IN_1: U3.11 (PA1), U4.21 (AIN1)
MOT_IN_2: U3.12 (PA2), U4.22 (AIN2)
MOT_IN_PWM: U3.10 (PA0), U4.23 (PWMA)
MOT_OUT_1: J2.1, U4.1 (AO1), U4.2 (AO1)
MOT_OUT_2: J2.2, U4.5 (AO2), U4.6 (AO2)
NRST: C8.1, J5.5, U3.7 (NRST)
unnamed: C4.1, U1.4 (BP)
unnamed: D1.2 (A), L1.1, U2.1 (SW)
unnamed: D4.2 (A), R4.2
unnamed: J1.4 (ID), R1.1
unnamed: R3.2, RV1.2, U2.3 (FB)
unnamed: R5.1, U3.44 (BOOT0)
POT: J3.2, U3.18 (PB0)
STBY: U3.13 (PA3), U4.19 (STBY)
SWCLK: J5.3, U3.37 (PA14)
SWDIO: J5.1, U3.34 (PA13)
TOUCH_SENSE: J4.1, U3.41 (PB5)
USB_DN: J1.2 (D-), U3.32 (PA11)
USB_DP: J1.3 (D+), R2.2, U3.33 (PA12)
VBUS: D2.2 (A), J1.1 (VBUS)
VPP: D3.2 (A), J5.4

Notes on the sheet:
3.3V REGULATOR
~~47k
10V BOOST
Id = sqrt(Iout * Imax)
Vout = 0.6 * (1 + RV1 / R2)
Recommended: 4.7uH - 22uH
POWER PROTECTION
CONNECTORS
USB CONNECTOR
MOTOR DRIVER
CLOSE TO MCU
MECHANICAL
DECOUPLING

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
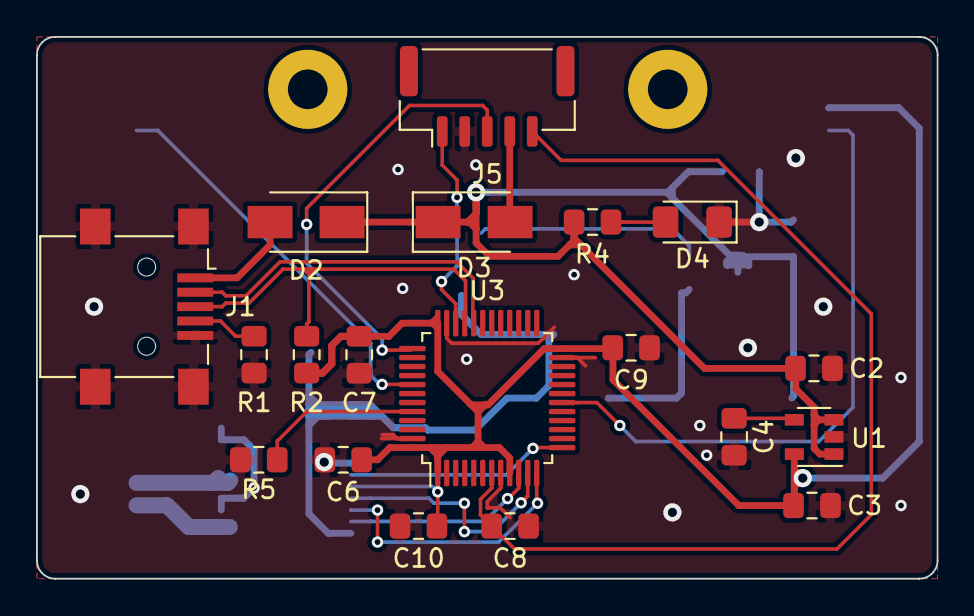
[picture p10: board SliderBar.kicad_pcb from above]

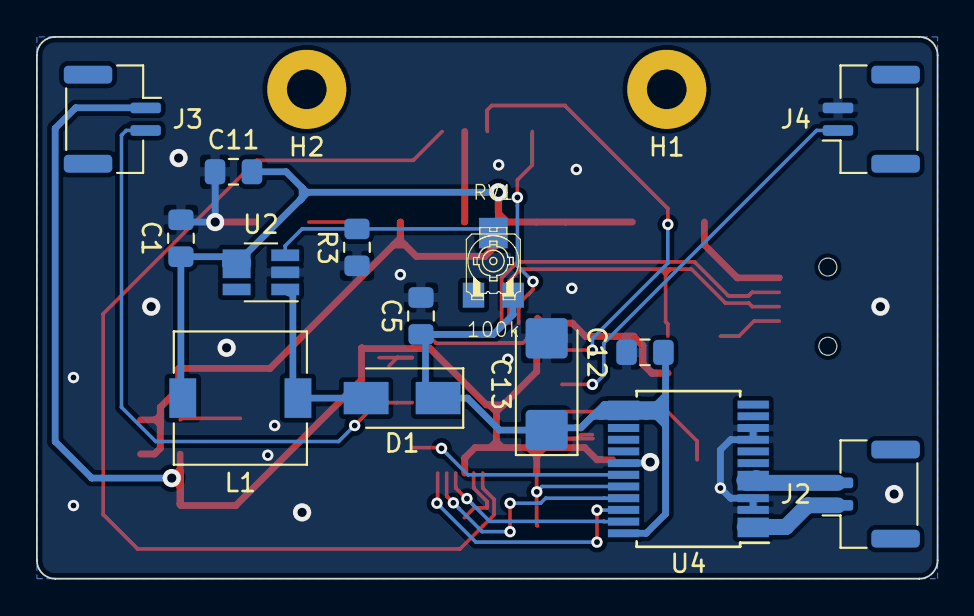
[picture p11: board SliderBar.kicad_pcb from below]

Board: 2 copper layers, 50.0 x 30.1 mm, 35 parts (16 on the bottom side), 25 nets.

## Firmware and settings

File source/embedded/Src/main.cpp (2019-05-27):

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

/* Includes ------------------------------------------------------------------*/
#include "main.h"

/* USER CODE BEGIN Includes */
#include <USB/CDC.h>
#include <cstring>
/* USER CODE END Includes */

ADC_HandleTypeDef hadc;

CRC_HandleTypeDef hcrc;

TIM_HandleTypeDef htim2;

void SystemClock_Config(void);
static void MX_GPIO_Init(void);
static void MX_ADC_Init(void);
static void MX_CRC_Init(void);
static void MX_TIM2_Init(void);
/**
 * @brief  The application entry point.
 * @retval int
 */
int main(void)
{
    /* USER CODE BEGIN 1 */
    usb::CDC cdc;
    /* USER CODE END 1 */

    /* MCU Configuration------------------------------------------------------*/

    /* Reset of all peripherals, Initializes the Flash interface and the Systick. */
    HAL_Init();

    /* Configure the system clock */
    SystemClock_Config();

    /* Initialize all configured peripherals */
    MX_GPIO_Init();
    MX_ADC_Init();
    MX_CRC_Init();
    MX_TIM2_Init();
    /* USER CODE BEGIN 2 */
    // This replaces the MX_USB initialization
    cdc.initialize();
    /* USER CODE END 2 */

    /* Infinite loop */
    /* USER CODE BEGIN WHILE */
    while (1) {
        /* USER CODE END WHILE */
        /* USER CODE BEGIN 3 */
    }
    /* USER CODE END 3 */
}

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


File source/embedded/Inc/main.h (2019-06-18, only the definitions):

#define B1_Pin GPIO_PIN_0
#define B1_GPIO_Port GPIOA
#define EXT_RESET_Pin GPIO_PIN_5
#define EXT_RESET_GPIO_Port GPIOC
#define LD3_Pin GPIO_PIN_6
#define LD3_GPIO_Port GPIOC
#define LD6_Pin GPIO_PIN_7
#define LD6_GPIO_Port GPIOC
#define LD4_Pin GPIO_PIN_8
#define LD4_GPIO_Port GPIOC
#define LD5_Pin GPIO_PIN_9
#define LD5_GPIO_Port GPIOC
#define USBF4_DM_Pin GPIO_PIN_11
#define USBF4_DM_GPIO_Port GPIOA
#define USBF4_DP_Pin GPIO_PIN_12
#define USBF4_DP_GPIO_Port GPIOA
#define SWDIO_Pin GPIO_PIN_13
#define SWDIO_GPIO_Port GPIOA
#define SWCLK_Pin GPIO_PIN_14
#define SWCLK_GPIO_Port GPIOA

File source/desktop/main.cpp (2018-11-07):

#include "mainwindow.h"
#include <QApplication>

int main(int argc, char* argv[])
{
    QCoreApplication::setOrganizationName("SliderBar");
    QCoreApplication::setOrganizationDomain("github.com/Haellsigh/SliderBar/");
    QCoreApplication::setApplicationName("SliderBar");

    QApplication a(argc, argv);
    MainWindow w;
    w.show();

    return a.exec();
}

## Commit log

2017-05-07 Base Arduino project using PlatformIO on Atom
2017-05-07 Working packets sending from arduino and receiving on pc
2017-05-13 Adding CRC on Arduino & code cleanup
2017-05-19 Motor control on Arduino
2017-05-19 Optimize PID & Motor driver
2017-05-21 Added ACK to protocol & prevent integral windup
    [main.cpp]
2017-05-28 Add PCB files
    [SliderBar.kicad_pcb, SliderBar.sch]
2017-06-03 Update PCB, Add resist_at basic support
    [SliderBar.sch]
2017-07-16 Improve PID Performances & Add tracking filter & graphs
    [SliderBar.kicad_pcb, SliderBar.sch]
2017-08-20 Added slots and signals for plugins
2018-01-18 Restarting circuit
    [SliderBar.kicad_pcb, SliderBar.sch]
2018-09-26 Deprecate all current progress
    [SliderBar-2018-07-10-21-03-14.sch, SliderBar-2018-07-10-21-03-49.sch, SliderBar-2018-07-11-23-53-13.sch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]
2018-09-26 Add motor driver doc
2018-10-01 Add STM32 doc
2018-10-01 Design schematic base
    [SliderBar.kicad_pcb, SliderBar.sch]
2018-10-14 Add step-up boost converter
    [SliderBar.sch]
2018-10-17 Update schematic
2018-10-17 Change project to STM32CubeHal, move USB_CDC to lib folder
2018-10-18 Begin TB6612FNG driver
2018-10-19 Add trimmer and replace MCU with STM32F072C8T6
    [SliderBar.sch]
2018-10-25 Fix includes, separate CDC from SliderBar
    [main.cpp]
2018-10-26 Change Voltage regulator to MIC5205
    [SliderBar.sch]
2018-10-30 Fix GND rotation
    [SliderBar.sch]
2018-10-31 Fix schottky diodes, finish schematic
    [SliderBar.sch]
2018-10-31 Create bare pcb
    [SliderBar.kicad_pcb]
2018-10-31 Fix footprints
    [SliderBar.sch]
2018-10-31 Define board size, place USB connector
    [SliderBar.kicad_pcb]
2018-10-31 Ignore backup pcb files
2018-10-31 Set clearance
    [SliderBar.kicad_pcb]
2018-10-31 Rotated mcu
    [SliderBar.kicad_pcb]
2018-10-31 Add GND to power class
    [SliderBar.kicad_pcb]
2018-10-31 Replace trimpot
    [SliderBar.kicad_pcb, SliderBar.sch]
2018-10-31 Layout: motor driver, boost converter, 3.3v regulator, debug header, MCU, USB tracks
    [SliderBar.kicad_pcb, SliderBar.sch]
2018-10-31 Update pcb
    [SliderBar.kicad_pcb]
2018-11-01 Change connector footprints to JST GH 1.25mm
    [SliderBar.kicad_pcb, SliderBar.sch]
2018-11-01 Add HTML bom
    [SliderBar.kicad_pcb]
2018-11-01 Add HTML bom, again
2018-11-02 Fix lot of footprints, Add mounting holes
    [SliderBar.kicad_pcb, SliderBar.sch]
2018-11-05 Move to source folder, and hardware folder
    [JST - GH - Thru - 2Pin - 1.25mm.stp, JST - GH - Thru - 3Pin - 1.25mm.stp, JST - GH - Thru - 5Pin - 1.25mm.stp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]
2018-11-20 Route some more traces
    [SliderBar.kicad_pcb]
2018-11-24 Add calibration to the GUI
2019-01-21 Trying to add LUA to project
    [SliderBar.kicad_pcb]
2019-01-22 Move mounting holes to a schematic bloc
    [SliderBar.sch]
2019-01-22 Add 3D CAD files for Motorized Pot, SliderBar PCB, Keyboard case
    [COMPOUND.CATPart, D_SMA.CATProduct, Frame.CATPart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]
2019-01-22 Assemble PCB and Potentiometer
    [COMPOUND.CATPart, D_SMA.CATProduct, EN_ISO_4032_M2_STEEL_GRADE_A_HEXAGON_NUT.CATPart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]
2019-01-22 Added DECOUPLING category to schematic
    [SliderBar.sch]
2019-01-22 Add schematic pdf
2019-01-22 Add schematic svg
2019-01-23 Final schematic update for prototype
    [SliderBar.kicad_pcb, SliderBar.sch]
2019-01-23 Setup PCB design rules and imported footprints
    [SliderBar.kicad_pcb]
2019-01-23 Fix potentiometer wiring, move Nelib library outside of project
    [JST - GH - Thru - 2Pin - 1.25mm.stp, JST - GH - Thru - 3Pin - 1.25mm.stp, JST - GH - Thru - 5Pin - 1.25mm.stp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]
2019-01-23 Add touch sense connection
    [SliderBar.sch]
2019-01-23 Fix capacitor valuee
    [SliderBar.sch]
2019-01-23 Add some 3D models from internet, fix some things
    [SliderBar.CATProduct, SliderBar.kicad_pcb, SliderBar.sch]
2019-01-24 Removed USB DP/DM resistors & Placed connectors
    [SliderBar.kicad_pcb, SliderBar.sch]
2019-01-24 Placed some components, fixed schematic
    [SliderBar.kicad_pcb, SliderBar.sch]
2019-01-25 Placed front components
    [SliderBar.kicad_pcb]
2019-01-25 Placed back components
    [SliderBar.kicad_pcb]
2019-01-25 Finished prototype PCB & 3D
    [COMPOUND.CATPart, COMPOUND_1.CATPart, CP_EIA-6032-28_Kemet-C.CATProduct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]
2019-05-26 Replace PlatformIO embedded project with CMake project with STM32CubeMX
    [embedded.ioc, main.cpp]
2019-06-08 Add base STM32CubeMX project with working USB comms
2019-06-08 Archive the current hardware files
    [COMPOUND.CATPart, COMPOUND_1.CATPart, CP_EIA-6032-28_Kemet-C.CATProduct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]
2019-06-08 Remove KiCad files from .gitignore
    [SliderBar-2018-09-26-20-29-46.sch]
2019-06-08 Update gitignore for KiCad
2019-06-09 Add STM32F072C8 MCU
    [STM32F0_Products.xlsx, SliderBar.kicad_pcb, SliderBar.sch]
2019-06-09 Change schematic sheet size to A3
    [SliderBar.sch]
2019-06-09 Add ULDO 3.3V regulator
    [SliderBar.sch]
2019-06-09 Add power protection diodes
    [SliderBar.sch]
2019-06-10 Add decoupling caps
    [SliderBar.sch]
2019-06-11 Add USB connector
    [SliderBar.sch]
2019-06-11 Add motor driver with current limiting
    [SliderBar.sch]
2019-06-11 Remove units from passive components values
    [SliderBar.sch]
2019-06-11 Add current limits calculations
    [SliderBar.sch]
2019-06-18 Ignore STM32CubeMX generated files
2020-06-09 Start a fresh repository
    [COMPOUND.CATPart, COMPOUND_1.CATPart, CP_EIA-6032-28_Kemet-C.CATProduct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]
2020-11-19 Revert "Start a fresh repository"
    This reverts commit fbaef52d0d564c90902da6cbc93ca921747f7037.
    [COMPOUND.CATPart, COMPOUND_1.CATPart, CP_EIA-6032-28_Kemet-C.CATProduct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]

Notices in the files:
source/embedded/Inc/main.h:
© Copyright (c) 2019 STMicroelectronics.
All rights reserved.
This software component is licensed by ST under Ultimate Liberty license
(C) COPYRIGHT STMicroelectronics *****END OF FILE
